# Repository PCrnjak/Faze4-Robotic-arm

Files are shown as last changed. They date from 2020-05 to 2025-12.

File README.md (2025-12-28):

   
# Faze4-Robotic-arm

 

https://source-robotics.com

Join discord community: https://discord.com/invite/prjUvjmGpZ 
Faze4 is small fully 3d printable Open source 6 axis robotic arm. It is functionally and esthetically similar to robotic arms in industry but is aimed for research, education and 
anyone interested in making his own robot arm. 
Main "selling points" of this arm that separate it from other DIY arms are:

* It is cheap <1000 dollars.
* Uses 3D printed cycloidal gearboxes which have low backlash and can be repaired really easy.
* All wires are hidden giving it clean design.

Whole arm has around 1000 parts (including screws and bearings) and weights around 15 kg.

# Check the arm in action!
Check the arm in action ! (https://www.youtube.com/watch?v=ye37Mpj5qCQ)

# Where to start? 

To build this robotic arm follow [Building instructions](https://github.com/PCrnjak/Faze4-Robotic-arm/blob/master/Assembly%20instructions%203.1.pdf). All general info about robotic arm is in [DOCS](https://faze4-robotic-arm-docs.readthedocs.io/en/latest/). Building instructions and DOCS go hand in hand and you need to follow both to build this arm. Building instructions are about general mechanical assembly while DOCS contain ALL info ( Electrical wiring, Low level setup, High level ROS and Matlab, tips ...).

# Contents:

- [Building instructions](https://github.com/PCrnjak/Faze4-Robotic-arm/blob/master/Assembly%20instructions%203.1.pdf)
- [BOM](https://github.com/PCrnjak/Faze4-Robotic-arm/blob/master/BOM_7_11_2023.xlsx) 
- [DOCS](https://faze4-robotic-arm-docs.readthedocs.io/en/latest/) Contains ALL info about the arm.
- [URDF files](https://github.com/PCrnjak/Faze4-Robotic-arm/tree/master/URDF_FAZE4) 

# Where to see more Faze4 robotic arm?
- [Youtube](https://www.youtube.com/channel/UCp3sDRwVkbm7b2M-2qwf5aQ)
- [Hackaday](https://hackaday.io/project/167247-faze4-robotic-arm)
- [DOCS](https://faze4-robotic-arm-docs.readthedocs.io/en/latest/)
- [Instagram](https://www.instagram.com/source_robotics/)

# ⚠️ Safety, Liability & Disclaimer

This project includes experimental software, hardware designs, and assembly documentation that are still under development and may contain bugs, errors, or incomplete features.
By using, building, or modifying this project, you acknowledge and agree that:
* You use this project entirely at your own risk
* You are solely responsible for safe assembly, testing, and operation
* No guarantee is made regarding correctness, safety, or reliability
* The authors are not responsible for any damage, injury, or loss resulting from the use or misuse of this project 
* Hardware performance and safety depend on user assembly, component quality, calibration, and handling, which cannot be guaranteed

This project is provided “as is.” If you choose to build a device yourself using these files, designs, or instructions, you do so without any warranties or guarantees, including regarding safety, reliability, or suitability for any particular purpose.

# Support the project

This project is entirely open source and free for all to use. Any support, whether through donations or advice, is greatly appreciated. Thank you!

 


# Project is under MIT Licence

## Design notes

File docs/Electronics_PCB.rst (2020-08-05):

Electronics, PCB and wiring
===========================

.. meta::
   :description lang=en: info about Electronics and PCB.
   
All electronics can also be bought from ebay and similar sites. I used cheap stepper drivers from ebay but you can buy any stepper driver that can supply enough current for the steppers.

Check how i wired my arm in this file: FAZE4 Robotic arm electronics setup.pdf on github page:
https://github.com/PCrnjak/Faze4-Robotic-arm

.. Tip::

   From experience i found out that cheaper stepper drivers tend to make more noise, so if you want quiet robot arm buy more expensive drivers. I found ones from stepperonline good.

PCB V1
------------
This PCB is first version and has some errors that will be fixed in revision 2.
Board was created in Altium Circuitmaker and all files can be found here:

.. Warning::

  I recommend waiting for next version since this one has alot of errors.

* `All files for PCB`_

.. _All files for PCB: https://github.com/PCrnjak/Faze4-Robotic-arm/blob/master/Distribution_PCB.zip

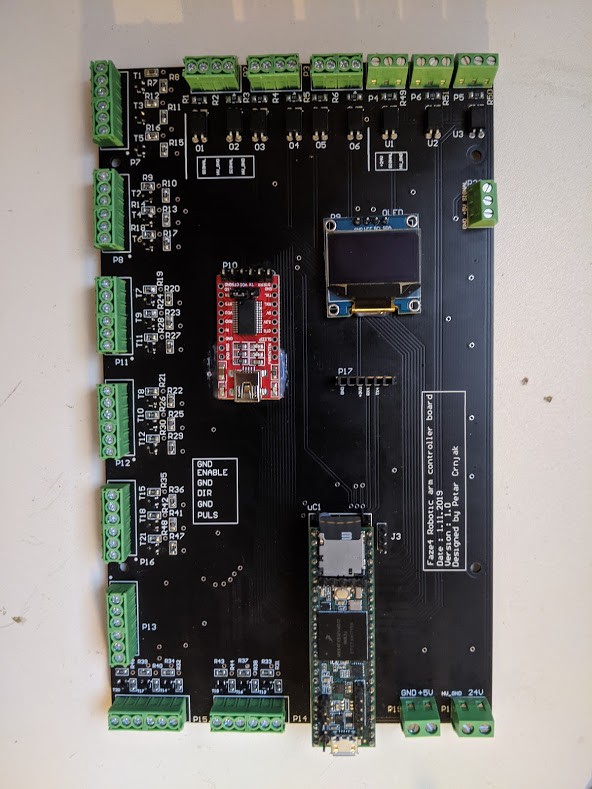
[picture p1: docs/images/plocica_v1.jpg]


Upper section of PCB are Inputs for limit switches and inductive sensors. All inputs on top are isolated with optocouplers. I did that since all wires of the arm are going thru same spot, that means "high voltage" stepper wires were near low voltage limit switch wires. That caused problems where steppers induced enough voltage on limit switch wires to trigger interrupts on teensy. That is why limit switches and sensors are connected to 24v.

left side is for stepper outputs. There are also 2 stepper outputs on bottom right side.

Bottom right side has 5V input and 24V input. You need both for arm to work. In the middle we have few extra serial ports and OLED display.

When wiring stepper drivers to the PCB i used TB6600  driver pinout as reference.I planned for all drivers to be connected like picture below. HIGH signal on ENABLE + pin would enable stepper drivers. Now i made some mistakes and not all drivers can be connected like that.

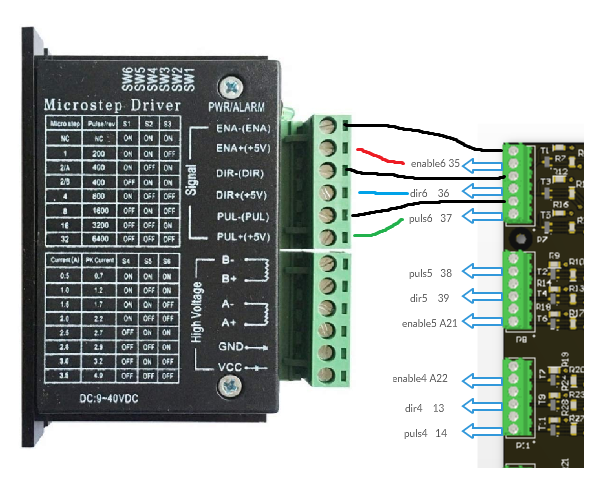
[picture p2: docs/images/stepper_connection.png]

    
Now i made some mistakes and not all drivers can be connected like that. In picture below you can see how to connect all drivers. As you can see for joint 5 (connector below top one) i switched enable and puls pins. That means that puls5 pin ( pin 38 on teensy) is connected to puls pin on stepper driver. I also skipped Port that has no 5V level shifter since it didnt work well.

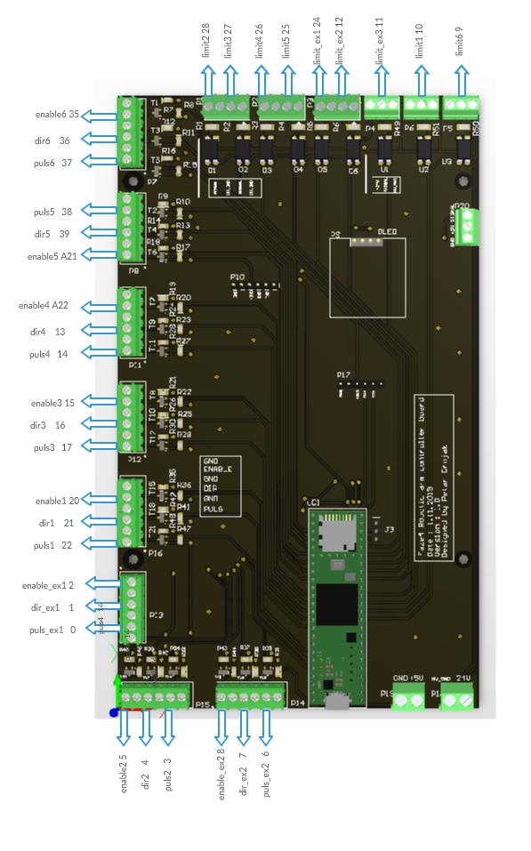
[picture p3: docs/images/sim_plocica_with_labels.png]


After wiring all dir,puls and enable pins you are left with power pins on stepper driver and A- A+ B- B+ Pins. Those are quite straightforward. 
Pins that have ext in name are extra pins that are now used in my version of arm.

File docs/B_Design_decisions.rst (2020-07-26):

Design decisions
===========================

.. meta::
   :description lang=en: Design decisons that were made when designing faze4 arm.

Number of axis
--------------

I went with 6 axis because with 6+ axis we can reach same dot in space with different orientations.
Both pictures show arm at position x=0.3m , y=0.3m and z=0.2m but as you can see orientations are different. 

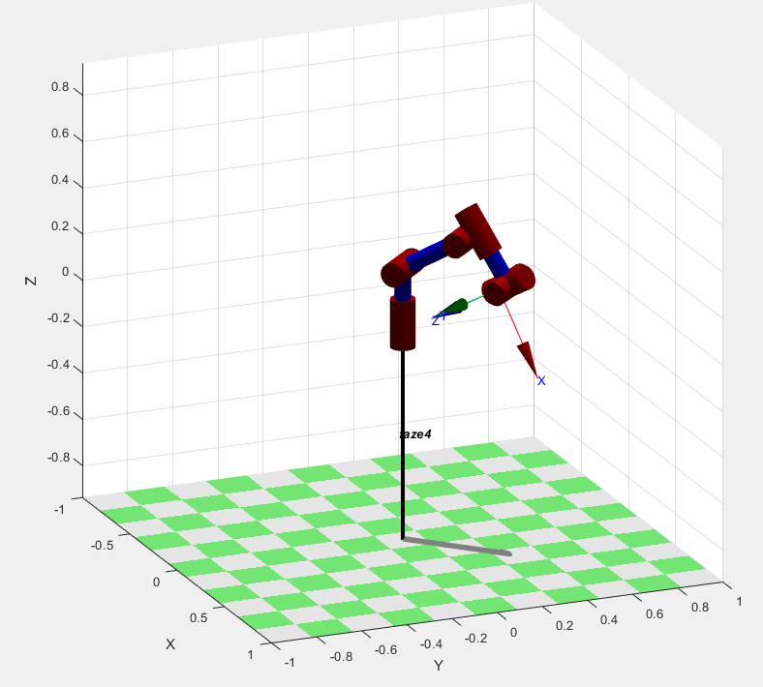
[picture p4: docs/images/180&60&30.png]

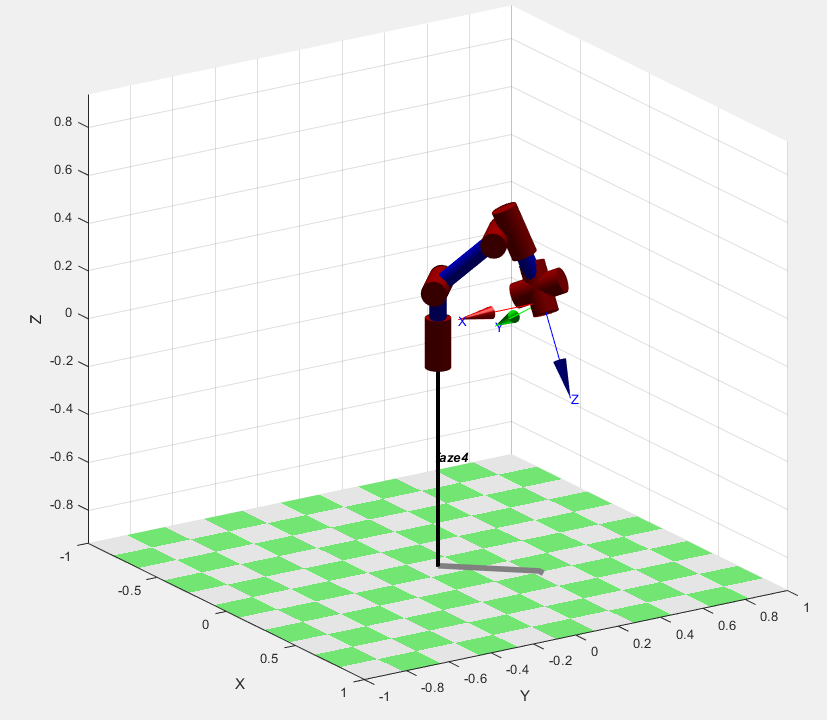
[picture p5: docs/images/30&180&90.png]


Spherical wrist
---------------

This arm uses so called spherical wrist. Spherical wrist is configuration of joints where axes of rotation for joints 4,5,6 intersect.
You can see that in picture below. It is complicated mechanical system that in turn simplifies solving inverse kinematics for robot arm. You will see this configuration in a lot industrial robot arm. 

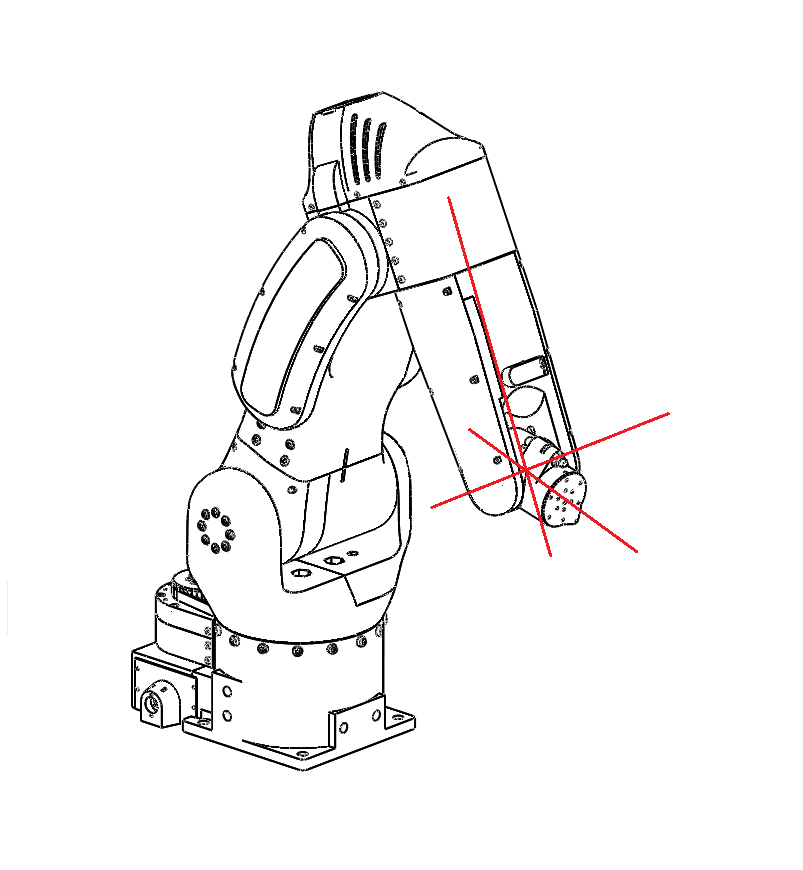
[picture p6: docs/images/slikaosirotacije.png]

    
All wires are routed thru the middle of the arm and cant be seen.

Cycloidal reducer
-----------------

Why cycloidal reducers?

* They are really easy to 3d print
* can have large reduction ratio
* cheap
* low backlash even when 3d printed

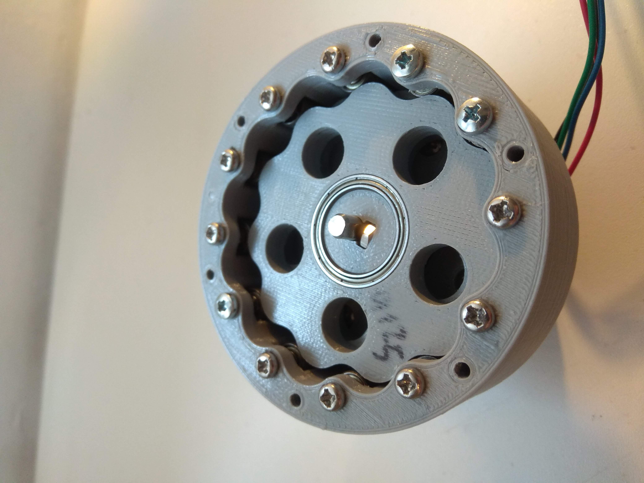
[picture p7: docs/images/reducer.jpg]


.. note::
   When 3d printing them there are few things to keep in mind but that is discussed in sections troubleshooting and printing.

Motor position
--------------

Firstly i wanted to move all motors to the base of the arm to reduce weight each motor should carry. First idea was to just copy the design of this(link) kuka arm. I decided against that design and just went with probably most basic design where every motor is directly on the joint of actuation ( Except for joint 5 that i moved a little bit away).This is not good idea actually and if I was redesigning this arm I would try to move at least joint 3 to the bottom of the arm, but what is done is done.

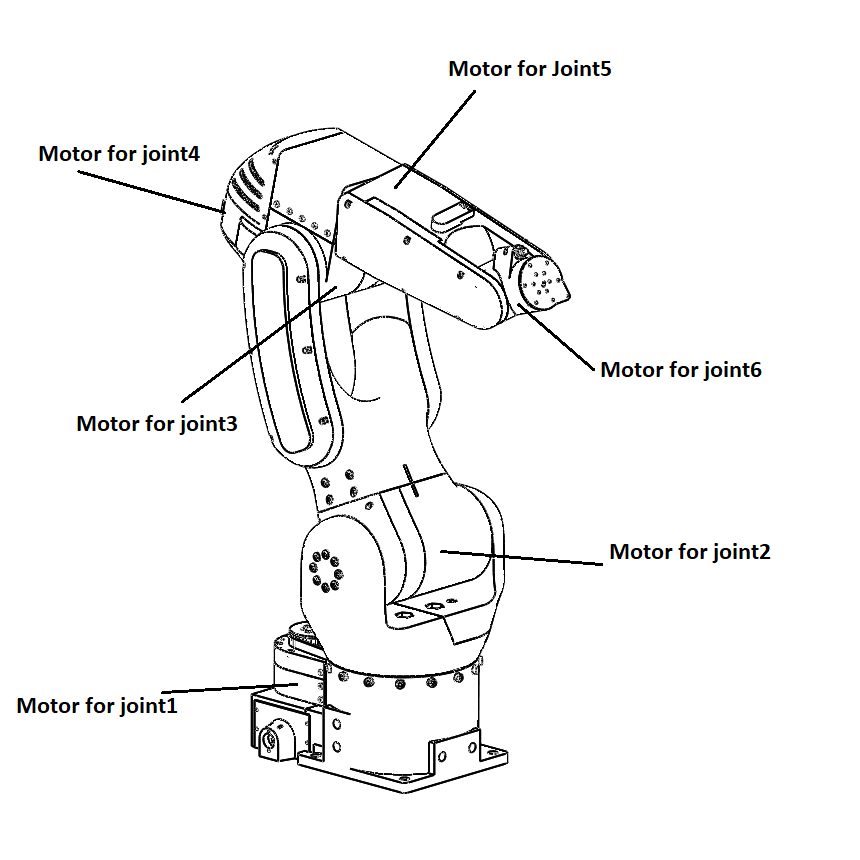
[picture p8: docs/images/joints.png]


Joints 1,4 and 5 use belts in addition to cycloidal reducers. Belts are mostly used to offset the place where joint will be rotating so that we can route wires thru the body of robot. They also give some additional reduction ratio. For example Joint 1 has 15:1 cyclo but with belt our reduction ratio jumps to 25:1.

Reduction ratios:
-----------------

* Joint 1 -> 15:1 cycloidal reducer and 5:3 belt reduction = combined resulting in 25:1 reduction
* Joint 2 -> 27:1 cycloidal reducer
* Joint 3 -> 15:1 cycloidal reducer
* Joint 4 -> 11:1 cycloidal reducer and 28:26 belt reduction = combined resulting in 11.846153:1 reduction 
* Joint 5 -> 11:1 cycloidal reducer and 1:1 belt reduction = combined resulting in 11:1 reduction
* Joint 6 -> 19.19:1 planetary reducer

Belts
-----------------

* Joint 1 belt is HTD 5M 490 mm timing belt 10 mm wide and needs to be tightened with bearings
* Joint 4 belt is HTD 5M 430 mm timing belt 10 mm wide does not need to be tightened
* Joint 5 belt is HTD 5M 285 mm timing belt 10 mm wide and needs to be tightened with bearings

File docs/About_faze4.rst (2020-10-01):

About Faze4
===========================

.. meta::
   :description lang=en: General info about Faze4 robotic arm.

General info
------------

Faze4 robotic arm came to be when i made a working 3d printable cycloidal gearbox and saw some potential in it. After that i designed whole arm around it. It uses 6 stepper motors, so it is a 6 axis robot arm. While designing this arm i focused on low backlash and good design of arm. All wires are hidden and arm is really rigid even tho it is 3d printed. Total cost of the arm is around 1000 - 1500 dollars.

.. note::

    This project is still work in progress. Part that is work in progress is control cabinet, that means that the arm can be built and it     will work without the cabinet.
    
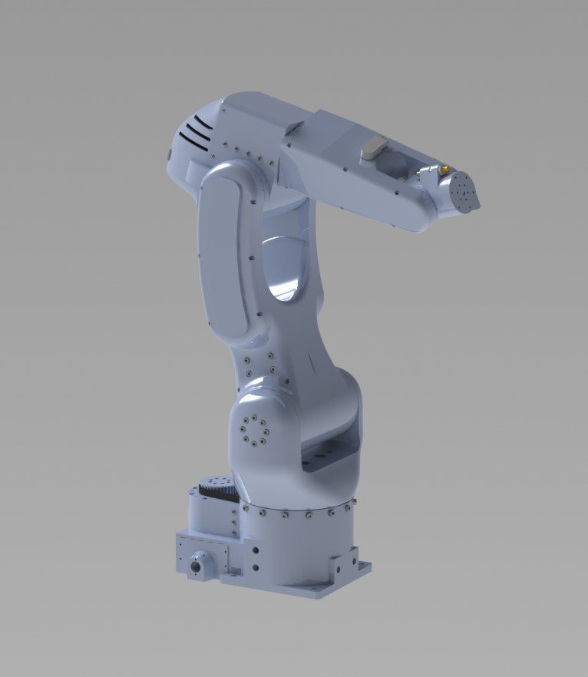
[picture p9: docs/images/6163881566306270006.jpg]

    
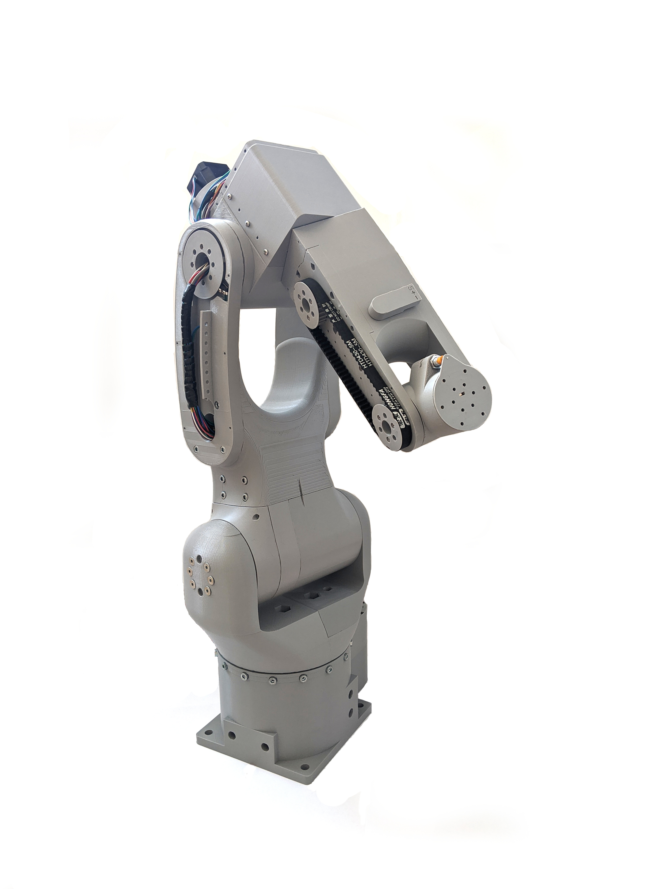
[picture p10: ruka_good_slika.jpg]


Esthetic design was inspired by FANUC’s LR Mate 200iD. 
Goal was also to hide all wires in the arm like most industrial arms do. 
Only visible wires (or pipes) would be ones for gripper. 

Weight of the arm is around 14-15 kg , but it can be reduced by printing with less infill.

Low level control for the arm runs on teesny 3.5, while high level (inverse kinematics, simulations) are only on Matlab code atm, but I am working on ROS implementation and porting my Matlab code to Python.

Table of contents
-----------------

On this read the docs page you will find:

* How is arm desinged and desing decisions
* Printing tips
* Electronics guide and PCB
* Building instructions for the arm
* All code and programs used
* How to test and troubleshoot
* Sources 
* Where to buy parts

Check the arm in action !
-------------------------

.. raw:: html

    <div style="text-align: center; margin-bottom: 2em;">
    <iframe width="100%" height="350" src="https://www.youtube.com/embed/-qTVx23o6C0?rel=0" frameborder="0" allow="autoplay; encrypted-media" allowfullscreen></iframe>
    </div>

Support the project
-------------------

This project is completely Open source and free to all and I would like to keep it that way, so any help 
in terms of donations or advice is really appreciated. Thank you!

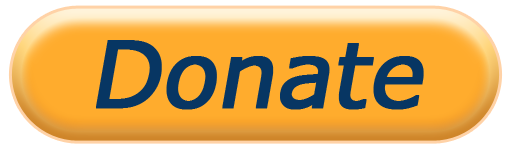
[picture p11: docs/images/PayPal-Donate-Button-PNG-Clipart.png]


Thanks to the:
--------------
* `Peter Corke for his amazing robotics toolbox for Matlab`_
* `Maximilian_Schommer for his cycloidal drive generator`_

.. _Peter Corke for his amazing robotics toolbox for Matlab: https://petercorke.com/toolboxes/robotics-toolbox/
.. _Maximilian_Schommer for his cycloidal drive generator: https://forum.onshape.com/discussion/7567/cycloidal-gear-generator

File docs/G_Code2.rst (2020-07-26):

High level code
===========================

.. meta::
   :description lang=en: info about Code.
   
High level code does all calculations and simulations. It will usually run on the PC since it will be doing a lot of
math and matrix multiplications. It will use some kind of inverse kinematics solver that will generate joint angles and speeds.
Again, gross simplification, but we will talk more about it later.

All code is in github repository.

Matlab code for testing in live script
---------------------------------------

 Matlab trajectory planning
----------------------------

ROS  
----

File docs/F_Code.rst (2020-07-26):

Low level code
===========================

.. meta::
   :description lang=en: info about Code.
   
Code for this robotic arm can be devided in 2 parts:

* Low level code
* High level code

Low level code is code that runs on our microcontroller (in our case teensy 3.5).
Its main purpose is to receive information from high level code and transform that information 
into useful signals for stepper drivers. That is a gross simplification, but codes used 
will be explained in more detail below.

All code is in github repository.

Tennsy environment setup
------------------------

Teensy low level code for testing in Matlab(live script)
--------------------------------------------------------

Teensy low level code for Matlab trajectory planning
----------------------------------------------------

Teensy low level code for ROS 
-----------------------------

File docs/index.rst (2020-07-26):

.. Read the Docs documentation master file, made by Petar Crnjak.

Faze4 Robotic arm documentation
==================================================

Contents:

.. toctree::
   :maxdepth: 2
   :glob:

   *

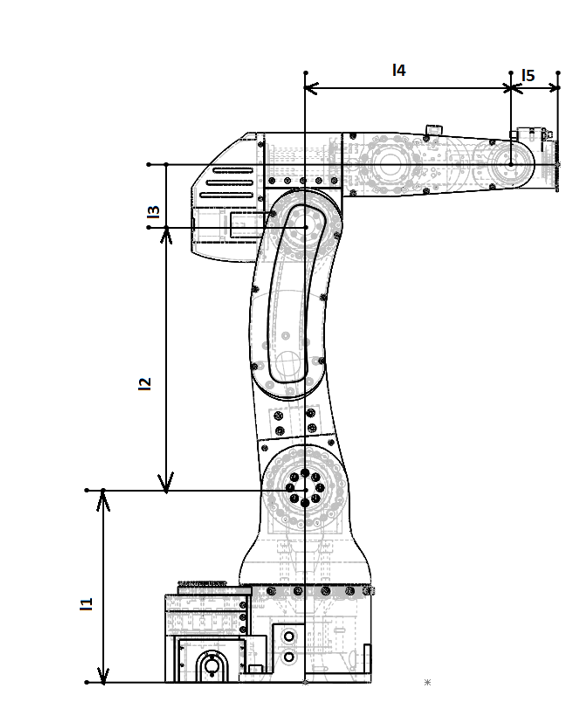
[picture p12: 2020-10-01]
docs/images/robot_dim.png

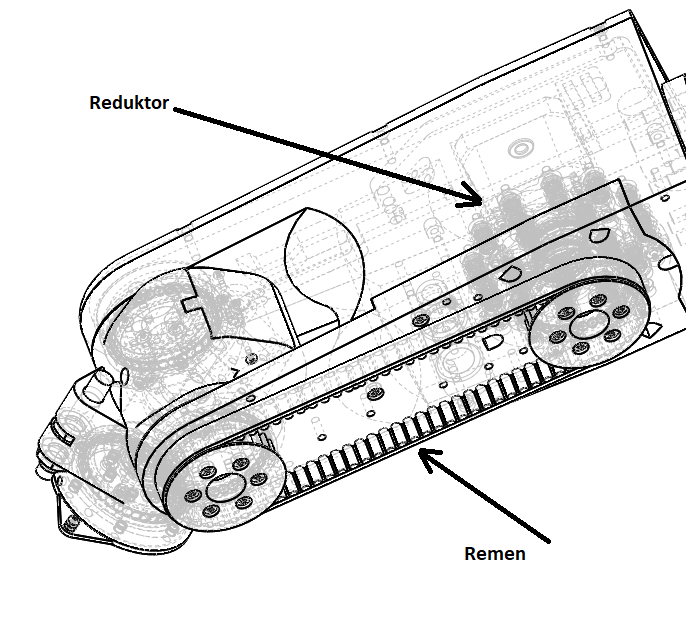
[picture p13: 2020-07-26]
docs/images/ReduktorREMEN.png

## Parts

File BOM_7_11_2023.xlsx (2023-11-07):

Some links included are affiliate links!
Screws: |  |  | 3D Printed parts:
diameter , lenght | Type | quantity | Name | quantity
M2 5mm screw | philips pan head | 3 | Joint 6 Output shaft | 1
M3 5mm screw | philips pan head | 12 | Wrist case | 1
M3 4mm set screw | Hex | 6 | Wrist cover | 1
M3 25mm screw | philips pan head | 64 | Forearm main case | 1
M2 8 mm screw | philips pan head | 8 | J5 ring rollers | 12
M3 20mm screw | philips pan head | 53 | 11:1 cyclo disc | 4
M3 10 mm screw | philips pan head | 54 | Eccentric shaft J5 | 1
M3 15mm screw | philips pan head | 54 | Servo gripper plug | 1
M5 30 mm screw | Hex socket cap | 13 | joint 5 output shaft | 1
M5 20 mm screw | Hex socket cap | 27 | joint 5 output spacers | 10
M5 8 mm screw | Hex socket cap | 12 | joint 5 switch trigger | 1
M3 30 mm screw | philips pan head | 52 | Forearm top cover | 1
M5 25 mm screw | Hex socket cap | 8 | J5 28 teeth pulley | 2
M2 10-12 mm screw | philips pan head | 7 | Joint 4 output shaft | 1
M5 40 mm screw | Hex socket cap | 10 | Joint 4 motor case | 1
M10 60 mm screw | Hex socket cap | 4 | J4 ring spacers | 12
 |  |  | Eccentric shaft J4 | 1
 |  |  | J4 cyclo output shaft | 1
 |  |  | joint 4 output spacers | 10
Bearings: |  |  | Joint 4 top cover | 1
Type | quantity | Link | Joint 3 main case | 1
Ball bearing 35x47x7 | 8 | Link (https://s.click.aliexpress.com/e/_DEiQvOn) | Joint 3 cover | 1
Ball bearing 3x8x4 | 200 | Link (https://s.click.aliexpress.com/e/_DdsVB2J) | 15:1 cyclo disc | 4
Ball bearing 17x23x4 | 4 | Link (https://s.click.aliexpress.com/e/_DExAkpt) | Joint 3 ring spacers | 32
Ball baering 15x28x7 | 6 |  | Joint 3 eccentric shaft | 1
Ball bearing 3x10x4 | 40 | Link (https://s.click.aliexpress.com/e/_Dl8fYKj) | Joint 3 output shaft | 1
Ball bearing 50x65x7 | 8 | Link (https://s.click.aliexpress.com/e/_DDV5uWF) | Joint 3 top cover | 1
Ball bearing 5x10x4 | 32 | Link (https://s.click.aliexpress.com/e/_DC7M02L) | Joint 4 offset | 1
Ball bearing 5x16x5 | 13 | Link (https://s.click.aliexpress.com/e/_Dl0Pgbd) | Joint 4 limit switch cover | 1
Ball bearing 20x27x4 | 2 | Link (https://s.click.aliexpress.com/e/_DCazrFD) | Joint 4 pulley 28 teeth | 1
 |  |  | 26 teeth Joint 4 pulley | 1
Other: |  |  | Fork | 1
Name | quantity | Link | Fork_motor | 1
M3 4mm brass inserts | 12 |  | Fork_wires | 1
M2 nuts | 2 |  | Joint 3 limit trigger | 1
M3 nuts | 6 |  | Joint 2 main case | 1
Inductive sensor | 2 | Link (https://s.click.aliexpress.com/e/_DE9VnjZ) | Joint 2 cover | 1
M8 nuts (usually included with sensor | 4 |  | Joint 2 eccentric shaft | 1
Nema 14 L=33mm w/19:1 gearbox | 1 | Link (https://www.omc-stepperonline.com/nema-14-stepper-motor-bipolar-l-33mm-w-gear-ratio-19-1-planetary-gearbox-14hs13-0804s-pg19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) | Joint 2 cyclo disc | 2
Nema 17 Bipolar 12V 42x42x40mm | 2 | Link (https://www.omc-stepperonline.com/nema-17-bipolar-45ncm-64oz-in-2a-42x42x40mm-4-wires-w-1m-cable-connector-17hs16-2004s1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) | Joint 2 ring spacer | 28
Pneumatic bulkhead connector 4mm xM12 thread | 2 |  | Joint 2 output shaft | 1
M12 nuts | 4 |  | Joint 2 top cover | 1
4mm pneumatic tube | 1 |  | Rotating base wires | 1
Micro limit switch | 3 |  | Rotating base motor | 1
HTD 5M 430 mm timing belt 10 mm wide | 1 |  | Joint 1 output shaft | 1
Nema 23 Bipolar 0.9deg 2.8A 2.5V 57x57x56mm | 1 | Link (https://www.omc-stepperonline.com/nema-23-bipolar-0-9deg-1-26nm-178-4oz-in-2-8a-2-5v-57x57x56mm-4-wires-23hm22-2804s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) | Joint 1 main case | 1
J4 beltv = HTD belt 5M 285 10mm wide | 1 |  | Joint 1 cover | 1
Nema 23 Bipolar 4A 2.26V 57x57x84mm | 1 | Link (https://www.omc-stepperonline.com/dual-shaft-nema-23-uni-bipolar-1-8deg-2-83nm-400-oz-in-4a-57x84mm-8-wires-23hs33-4008d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) | Joint 1 ring spacers | 32
M5 nuts | 15 |  | Joint 1 eccentric shaft | 1
M10 nuts | 4 |  | Joint 1 cyclo output shaft | 1
Roller limit switches | 2 |  | Joint 1 top cover | 1
Nema 23 Bipolar 1.5A 5.4V 57x57x56mm | 1 | Link (https://www.omc-stepperonline.com/nema-23-bipolar-1-8deg-1-16nm-164-3oz-in-1-5a-5-4v-57x57x56mm-4-wires-23hs22-1504s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) | Main base | 1
HTD 5M 490 mm timing belt 10 mm wide | 1 |  | 36 teeth pulley | 1
 |  |  | Ball bearing retainer | 1
 |  |  | Shaft blocker | 1
 |  |  | Forearm motor lid | 1
Total not 3d printed parts : | 764 |  | Forearm wires lid | 1
 |  |  | Elbow lid | 1
Total 3d printed parts : | 197 |  | Upper arm lid | 1
 |  |  | Rotating base lid | 1
Total parts | 961

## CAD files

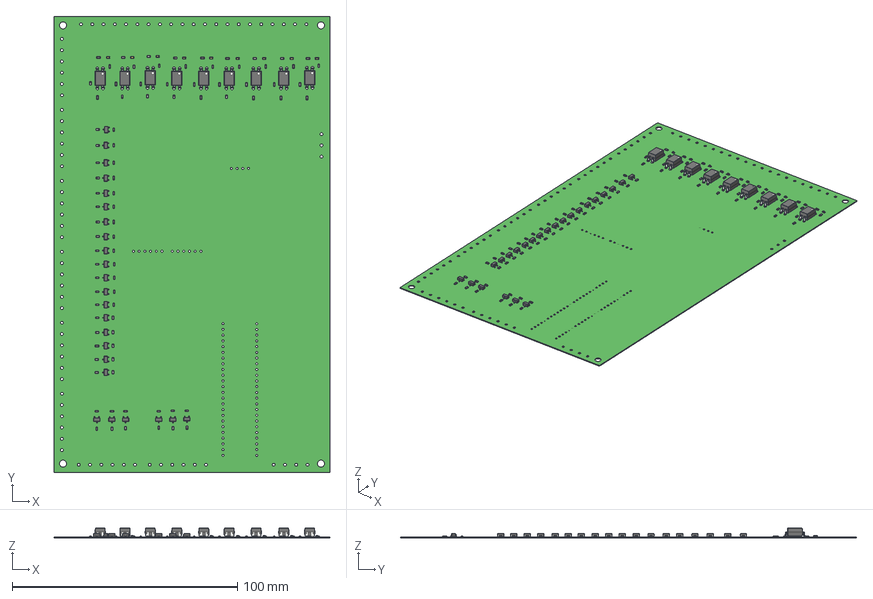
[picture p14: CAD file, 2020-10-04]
Faze4_DIST_board_v2_files/Faze4_dist_v2_STEP.step
122.5 x 202.5 x 4.26 mm
Board
0603_resistor x 84
LTV-817S x 9
LED_0603_Base_YELLOW x 9
LED_0603_Lens_YELLOW x 9
sot-23-3 x 24

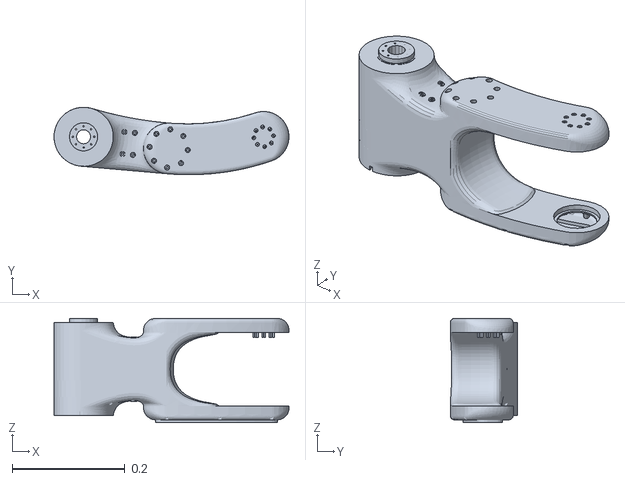
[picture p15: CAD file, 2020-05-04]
URDF_FAZE4/meshes/nadlaktica.STL
0.417 x 0.12 x 0.185

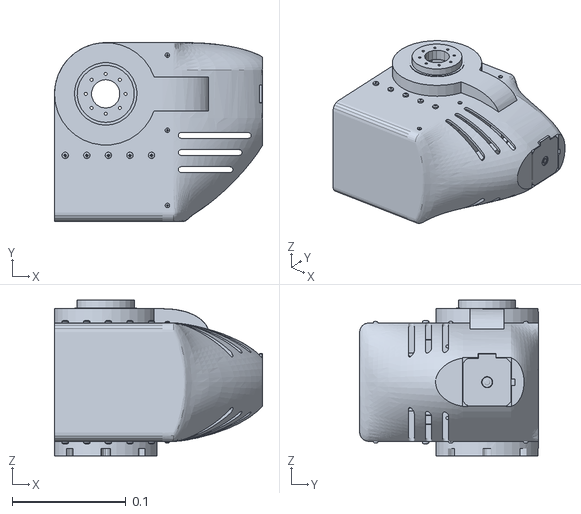
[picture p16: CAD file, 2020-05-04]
URDF_FAZE4/meshes/lakat.STL
0.183 x 0.157 x 0.137

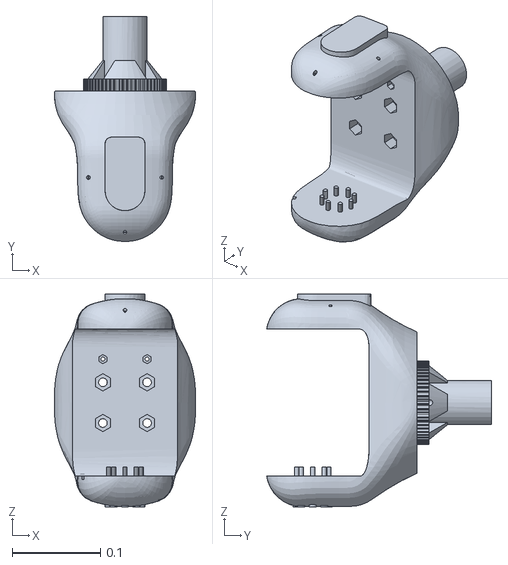
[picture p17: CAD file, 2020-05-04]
URDF_FAZE4/meshes/rotary_base.STL
0.16 x 0.254 x 0.241

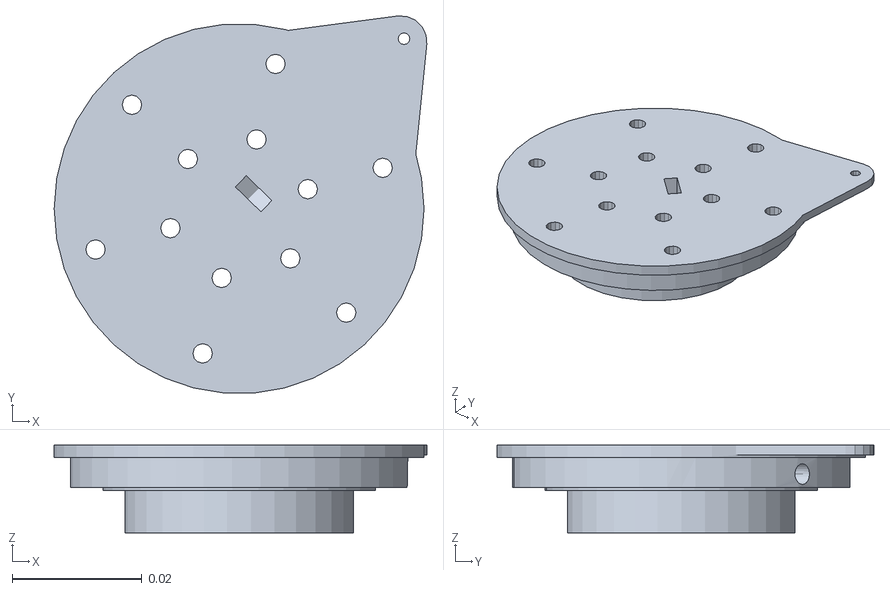
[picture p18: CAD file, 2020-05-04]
URDF_FAZE4/meshes/hvataljka.STL
0.0574 x 0.0581 x 0.0135

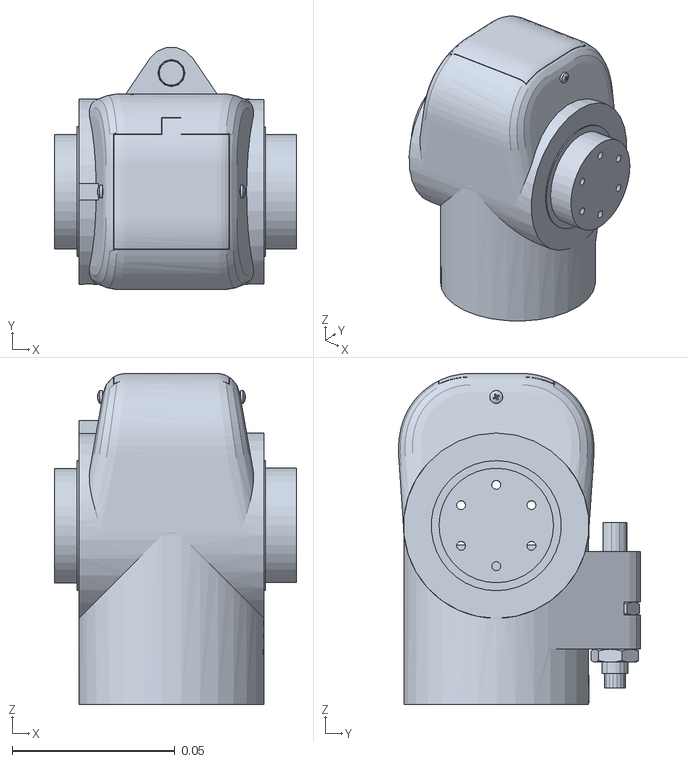
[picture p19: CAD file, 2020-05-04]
URDF_FAZE4/meshes/saka.STL
0.0745 x 0.0744 x 0.102

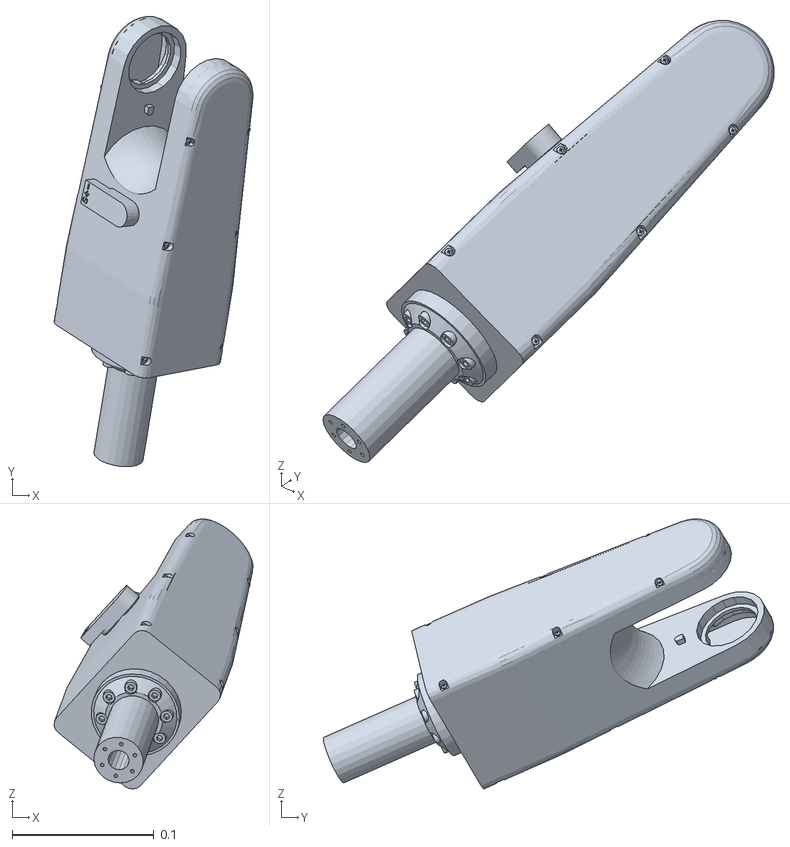
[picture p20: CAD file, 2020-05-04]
URDF_FAZE4/meshes/podlaktica.STL
0.14 x 0.318 x 0.191

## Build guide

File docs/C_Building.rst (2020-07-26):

Building 
===========================

.. meta::
   :description lang=en: Instructions and tips to build mechanical part of the arm.
   
.. note::

   All parts can be bought from ebay and similar online stores. I bought all steppers,drivers and PSUs from stepper online. You can buy    screws used for this arm in online stores but i sourced them locally and that was much cheaper. I also recommend to buy wires (you      will need them to extend stepper wires) locally since ones on ebay and similar stores are of questionable quality.

* `Full assembly instructions are here`_

.. _Full assembly instructions are here: https://github.com/PCrnjak/Faze4-Robotic-arm

BOM
------------
You can find bom in this excel document and in building instructions file. 

* `BOM FILE`_

.. _BOM FILE: https://github.com/PCrnjak/Faze4-Robotic-arm

.. Tip::

   I also recommend to buy more items like bearinngs and screws than you need since you might destroy or damage some in building            process.

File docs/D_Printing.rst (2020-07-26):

Printing
===========================

.. meta::
   :description lang=en: Printing tips.

Filament
------------

I recommend PETG since it can withstand larger temperatures then PLA and is easier to print then ABS. Since motors can heat up i think it is best choice.

Printer
------------

All parts are designed to be printed on Prusa MK2S, so if you have printer with build volume of 250x210x200 you are good to go.

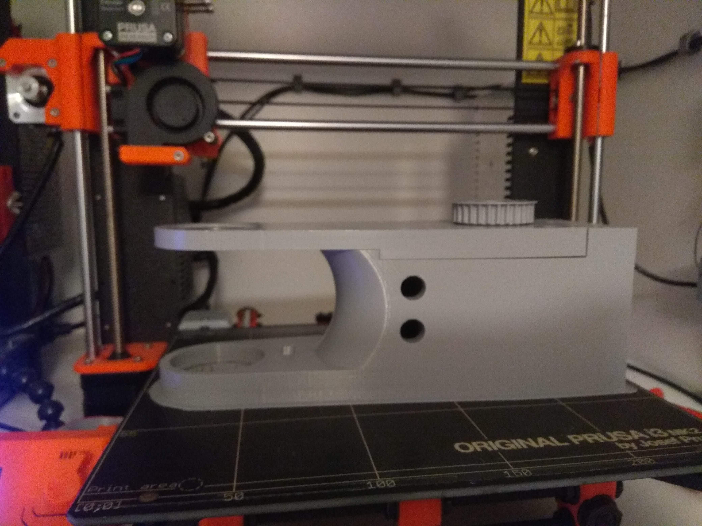
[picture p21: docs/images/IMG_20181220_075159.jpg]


Print settings and tips
------------------------

I printed all smaller parts with 0.15 layer height and all larger with 0.35 layer height.For infill try to stay in 25%-30% range. I used 3 outer perimeters and 7 top and 5 bottom layers.

.. Tip::

   When printing larger parts like: x x x , try to print at slower speeds and with small accelerations.Since those parts are really        large and heavy they tend to cause missing steps when reaching the end of 3d print due the inertia.

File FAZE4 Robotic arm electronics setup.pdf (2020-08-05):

FAZE4 Robotic arm electronics setup

So this is wiring guide for my setup of the arm. If you plan to build Faze4 robotic arm it might not look like this. Your wires might have different colour coding, different steppers…
So here i am going to explain some general tips.
- Microsteps for motors should be kept like ones in tables. If you change them change microstep values in software to.
- Adjust Peak current for your steppers. I used peak value of stepper drivers but actually we use RMS value of current so adjust to your RMS current!
- Voltage your stepper motor is rated
- Limit switch dir tells us what state needs to be on stepper driver DIR pin to initiate movement in DIRECTION TO HIT A LIMIT SWITCH ! This is really important! These values should be left as they are in this table. If you see your stepper is moving away from limit switch just switch any 2 wires of the same phase on stepper driver and that will change the direction. You can change it in software too but this method is easier.
- ENABLE tells us what state on enable pin of stepper drivers ENABLES the driver.
- Wires for my setup and Control pins are specific for my build of the arm.

ROBOT electronics setup

JOINT 6

Microstep | Current | Voltage | Limit switch DIR | ENABLE
400 | PK 0.7A | 24V | LOW | LOW

Wires for my setup: red,green,blue,yellow (A+,A-,B+,B-)
Control pins: GND,ENA+,GND,DIR+,PULS+

JOINT 5

Microstep | Current | Voltage | Limit switch DIR | ENABLE
400 | PK 1.2A | 24V | HIGH | ANALOG: 0

Wires for my setup: red,blue,green,black (A+,A-,B+,B-)
Control pins: GND,PULS+,GND,DIR+,ENA+

JOINT 4

Microstep | Current | Voltage | Limit switch DIR | ENABLE
400 | PK 1.2A | 24V | HIGH | ANALOG: 0

Wires for my setup: red,blue,black,green (A+,A-,B+,B-)
Control pins: GND,ENA+,GND,DIR+,PULS+

JOINT 3

Microstep | Current | Voltage | Limit switch DIR | ENABLE
400 | PK 2.2A | 24V | HIGH | LOW

Wires for my setup: red,blue,black,green (A+,A-,B+,B-)
Control pins: GND,ENA+,GND,DIR+,PULS+

JOINT 2

Microstep | Current | Voltage | Limit switch DIR | ENABLE
1600 | PK 2.7A | 36V | HIGH | LOW

Wires for my setup: red,yellow,orange,purple (B-,B+,A-,A+)
Control pins: PULS+,GND,DIR+,GND,ENA+

JOINT 1

Microstep | Current | Voltage | Limit switch DIR | ENABLE
1600 | PK 2.7A | 24V | HIGH | LOW

Wires for my setup: red,blue,black,green (A+,A-,B+,B-)
Control pins: GND,ENA+,GND,DIR+,GND,PULS+

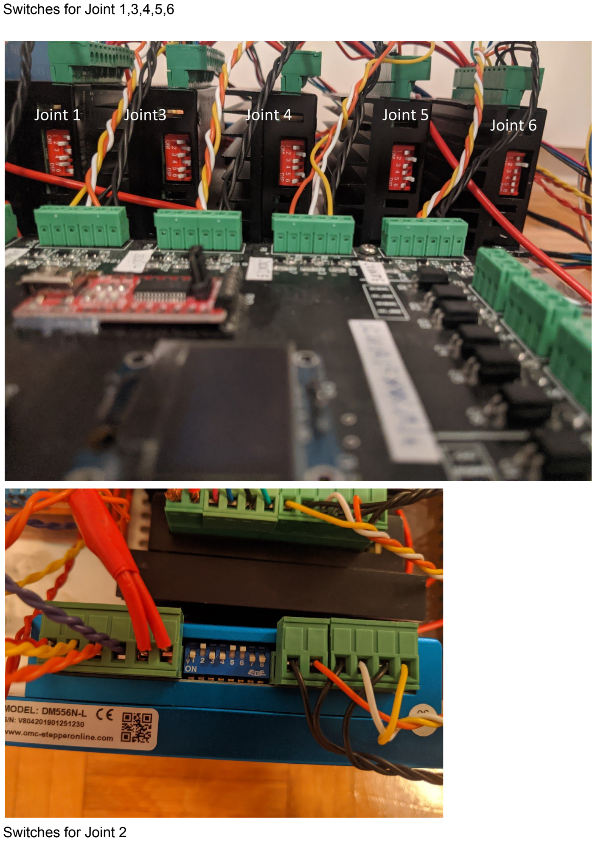
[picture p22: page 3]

Switches for Joint 1,3,4,5,6

Switches for Joint 2

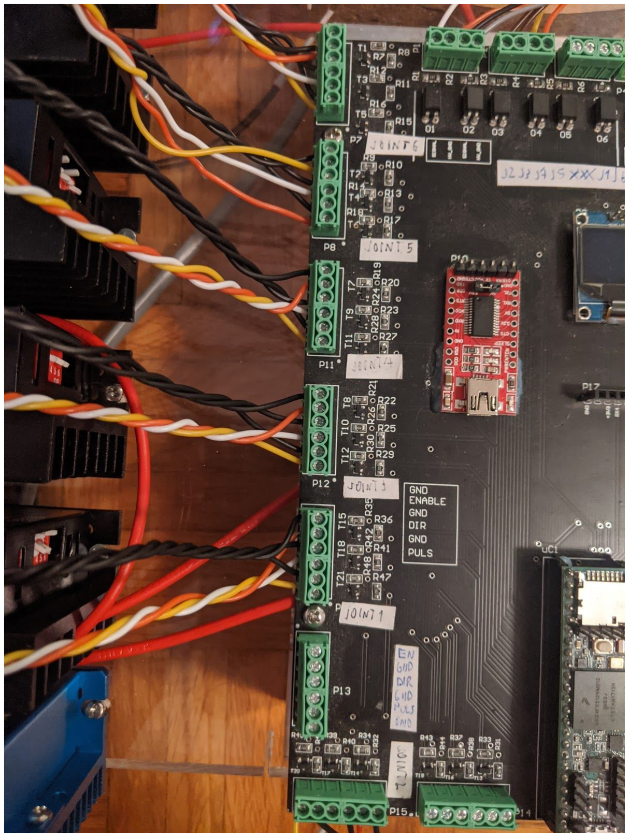
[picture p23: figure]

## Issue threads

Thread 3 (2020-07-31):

high-level help

i-make-robots, 2020-07-31:
Hi!  Your arm is gorgeous.  Would love to see some exploded diagrams or section diagrams in the documentation.

I have a visual simulator and firmware that should run IK for your robot and knows how to use acceleration for smoother motion.

https://github.com/MarginallyClever/Makelangelo-software is the firmware (supporting many kinematic models) and

https://github.com/MarginallyClever/Robot-Overlord is the software (gradient descent IK, simulation, etc)

I hope it helps!

PCrnjak, 2020-09-06:
I am really sorry i didnt see this. Yea i saw your robot - overlord software and i am planning to try it out, but first i want to get ROS working so it will take some time.
Anyway when i start working on it i will keep you updated, it looks great thx!

Closed 2024-03-13.

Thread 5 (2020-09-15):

thanks for your work

maokk, 2020-09-15:
I am almost print all the STL files and prepare for assemble . waiting for your low and high code release, thank you

Closed 2024-03-13.

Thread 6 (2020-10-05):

Wrong Bearing in BOM

Waldkaeuzchen, 2020-10-05:
Hello,
first off all, thank you for your amazing Work!

While searching for all parts I noticed that their seems to bin a Typo in the list: the ball bearings 50x67x7 are listed, but later on in the manual 50x65x7 is used, which doesnt appear in the BOM.

Greetings,
Waldkaeuzchen

Closed 2024-03-13.

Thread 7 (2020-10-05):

Building instructions link broken

maxymczech, 2020-10-05:
https://github.com/PCrnjak/Faze4-Robotic-arm/blob/master/Assembly%20instructions%203.0.pdf - this link in readme.md is 404 broken.

Closed 2024-03-13.

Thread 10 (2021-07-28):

STEP Files

MaxBareiss, 2021-07-28:
This robot arm is awesome and I'm trying to make one. Inductive sensors with an 8mm body are too expensive, so I bought ones with an 18mm body and I'd like to adapt the parts to the new hole size. Are the original CAD files or STEP format CAD files publically available for this project to make it easier to modify?

maokk, 2022-02-18:
I am also have  the  same problem, I am prepare to assemble this robot arm, but my joint3 stepper motor are a little bit different , its very ugly to cut after printed the Joint 3 cover.STL

Closed 2024-03-13.

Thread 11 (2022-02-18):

question about Joint 3 cover.STL

maokk, 2022-02-18:
thanks for your great job, I am now prepare to assemble this robot arm, but my joint3 stepper motor are a little bit different from yours, its very ugly to cut after printed the "Joint 3 cover.STL", so could you share this modified file? thanks

Closed 2024-03-13.

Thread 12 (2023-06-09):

Wild mesh origins

i-make-robots, 2023-06-09:
Hi!

I loaded the meshes into Robot Overlord today and I see the mesh origins are all over the place.  I'm unable to fix the files using the URDF numbers.

I would like please:

1. all arm parts share the same origin at the robot base center

OR

2. all arm parts have their correct local origin with Z axis matching the axis of rotation.

... and a DH parameter table that includes max/min joint range, D, R, Alpha, and Theta.

Example of wonky origin attached.  This model is also some distance off the floor.
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

Closed 2024-03-13.

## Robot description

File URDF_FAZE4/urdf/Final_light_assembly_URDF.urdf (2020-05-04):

<robot name="Final_light_assembly_URDF">
  <link name="base_link">
    <inertial>
      <origin xyz="0.0754452420016786 0.0706653851885525 0.174716050606158" rpy="0 0 0" />
      <mass value="1.75590983031249" />
      <inertia ixx="0.0106901651591523" ixy="1.2533292416581E-05" ixz="-1.78802486116636E-05" iyy="0.0121389538778755" iyz="-0.0001726147454493" izz="0.00523087609446992" />
    </inertial>
    <visual>
      <origin xyz="0 0 0" rpy="0 0 0" />
      <geometry>
        <mesh filename="package://Final_light_assembly_URDF/meshes/base_link.STL" />
      </geometry>
      <material name="">
        <color rgba="0.792156862745098 0.819607843137255 0.933333333333333 1" />
      </material>
    </visual>
    <collision>
      <origin xyz="0 0 0" rpy="0 0 0" />
      <geometry>
        <mesh filename="package://Final_light_assembly_URDF/meshes/base_link.STL" />
      </geometry>
    </collision>
  </link>
  <link name="rotary_base">
    <inertial>
      <origin xyz="3.6594E-07 -0.12491 -0.0091222" rpy="0 0 0" />
      <mass value="1.8968" />
      <inertia ixx="0.011703" ixy="6.2683E-07" ixz="2.7765E-07" iyy="0.010005" iyz="-0.00096832" izz="0.0065158" />
    </inertial>
    <visual>
      <origin xyz="0 0 0" rpy="0 0 0" />
      <geometry>
        <mesh filename="package://Final_light_assembly_URDF/meshes/rotary_base.STL" />
      </geometry>
      <material name="">
        <color rgba="0.79216 0.81961 0.93333 1" />
      </material>
    </visual>
    <collision>
      <origin xyz="0 0 0" rpy="0 0 0" />
      <geometry>
        <mesh filename="package://Final_light_assembly_URDF/meshes/rotary_base.STL" />
      </geometry>
    </collision>
  </link>
  <joint name="rotary_base" type="continuous">
    <origin xyz="0.075629 -0.21266 0.050734" rpy="-1.5708 -6.123E-17 -1.5708" />
    <parent link="base_link" />
    <child link="rotary_base" />
    <axis xyz="0 -1 0" />
  </joint>
  <link name="nadlaktica">
    <inertial>
      <origin xyz="0.11187 -0.011704 0.007695" rpy="0 0 0" />
      <mass value="3.097" />
      <inertia ixx="0.011686" ixy="0.0012432" ixz="-0.0018781" iyy="0.03891" iyz="-5.4012E-05" izz="0.032612" />
    </inertial>
    <visual>
      <origin xyz="0 0 0" rpy="0 0 0" />
      <geometry>
        <mesh filename="package://Final_light_assembly_URDF/meshes/nadlaktica.STL" />
      </geometry>
      <material name="">
        <color rgba="0.79216 0.81961 0.93333 1" />
      </material>
    </visual>
    <collision>
      <origin xyz="0 0 0" rpy="0 0 0" />
      <geometry>
        <mesh filename="package://Final_light_assembly_URDF/meshes/nadlaktica.STL" />
      </geometry>
    </collision>
  </link>
  <joint name="nadlaktica" type="continuous">
    <origin xyz="0 -0.20182 0" rpy="2.7756E-15 -1.3878E-15 -1.8111" />
    <parent link="rotary_base" />
    <child link="nadlaktica" />
    <axis xyz="0 0 1" />
  </joint>
  <link name="lakat">
    <inertial>
      <origin xyz="0.020310022580536 -0.0354589471585284 0.00171229454365077" rpy="0 0 0" />
      <mass value="1.2726491805247" />
      <inertia ixx="0.00430935066273582" ixy="-0.000472663673983171" ixz="2.10793692092687E-05" iyy="0.00388873322685888" iyz="-0.000102922808916268" izz="0.00512549454697952" />
    </inertial>
    <visual>
      <origin xyz="0 0 0" rpy="0 0 0" />
      <geometry>
        <mesh filename="package://Final_light_assembly_URDF/meshes/lakat.STL" />
      </geometry>
      <material name="">
        <color rgba="0.792156862745098 0.819607843137255 0.933333333333333 1" />
      </material>
    </visual>
    <collision>
      <origin xyz="0 0 0" rpy="0 0 0" />
      <geometry>
        <mesh filename="package://Final_light_assembly_URDF/meshes/lakat.STL" />
      </geometry>
    </collision>
  </link>
  <joint name="lakat" type="continuous">
    <origin xyz="0.32 0 0" rpy="3.1416 -6.3895E-16 -1.1753" />
    <parent link="nadlaktica" />
    <child link="lakat" />
    <axis xyz="0 0 -1" />
  </joint>
  <link name="podlaktica">
    <inertial>
      <origin xyz="0.015666 0.10444 0.04524" rpy="0 0 0" />
      <mass value="0.8658" />
      <inertia ixx="0.0043737" ixy="-0.00033248" ixz="-0.00029637" iyy="0.0017275" iyz="-0.0011009" izz="0.0039233" />
    </inertial>
    <visual>
      <origin xyz="0 0 0" rpy="0 0 0" />
      <geometry>
        <mesh filename="package://Final_light_assembly_URDF/meshes/podlaktica.STL" />
      </geometry>
      <material name="">
        <color rgba="0.79216 0.81961 0.93333 1" />
      </material>
    </visual>
    <collision>
      <origin xyz="0 0 0" rpy="0 0 0" />
      <geometry>
        <mesh filename="package://Final_light_assembly_URDF/meshes/podlaktica.STL" />
      </geometry>
    </collision>
  </link>
  <joint name="podlaktica" type="continuous">
    <origin xyz="0 -0.0735 0" rpy="-0.5648 -0.78173 1.7809" />
    <parent link="lakat" />
    <child link="podlaktica" />
    <axis xyz="0.14804 0.90477 0.39934" />
  </joint>
  <link name="saka">
    <inertial>
      <origin xyz="0.00102127447654127 0.00173769308862193 -0.00307332521672926" rpy="0 0 0" />
      <mass value="0.195660541483626" />
      <inertia ixx="0.000196163267087824" ixy="-1.19915207726741E-07" ixz="-4.99910323817217E-07" iyy="0.000195263940589931" iyz="9.07364788265256E-06" izz="0.000136132402412911" />
    </inertial>
    <visual>
      <origin xyz="0 0 0" rpy="0 0 0" />
      <geometry>
        <mesh filename="package://Final_light_assembly_URDF/meshes/saka.STL" />
      </geometry>
      <material name="">
        <color rgba="0.792156862745098 0.819607843137255 0.933333333333333 1" />
      </material>
    </visual>
    <collision>
      <origin xyz="0 0 0" rpy="0 0 0" />
      <geometry>
        <mesh filename="package://Final_light_assembly_URDF/meshes/saka.STL" />
      </geometry>
    </collision>
  </link>
  <joint name="saka" type="continuous">
    <origin xyz="0.037114 0.22683 0.10011" rpy="2.2965 -0.74045 -0.57161" />
    <parent link="podlaktica" />
    <child link="saka" />
    <axis xyz="-1 0 0" />
  </joint>
  <link name="hvataljka">
    <inertial>
      <origin xyz="0.00017222 0.00017758 0.00947" rpy="0 0 0" />
      <mass value="0.020284" />
      <inertia ixx="3.4622E-06" ixy="-9.927E-08" ixz="-2.2616E-08" iyy="3.4561E-06" iyz="-2.332E-08" izz="6.3508E-06" />
    </inertial>
    <visual>
      <origin xyz="0 0 0" rpy="0 0 0" />
      <geometry>
        <mesh filename="package://Final_light_assembly_URDF/meshes/hvataljka.STL" />
      </geometry>
      <material name="">
        <color rgba="0.79216 0.81961 0.93333 1" />
      </material>
    </visual>
    <collision>
      <origin xyz="0 0 0" rpy="0 0 0" />
      <geometry>
        <mesh filename="package://Final_light_assembly_URDF/meshes/hvataljka.STL" />
      </geometry>
    </collision>
  </link>
  <joint name="hvataljka" type="continuous">
    <origin xyz="0 0 -0.042312" rpy="-3.1416 2.5362E-15 0.2419" />
    <parent link="saka" />
    <child link="hvataljka" />
    <axis xyz="0 0 1" />
  </joint>
</robot>

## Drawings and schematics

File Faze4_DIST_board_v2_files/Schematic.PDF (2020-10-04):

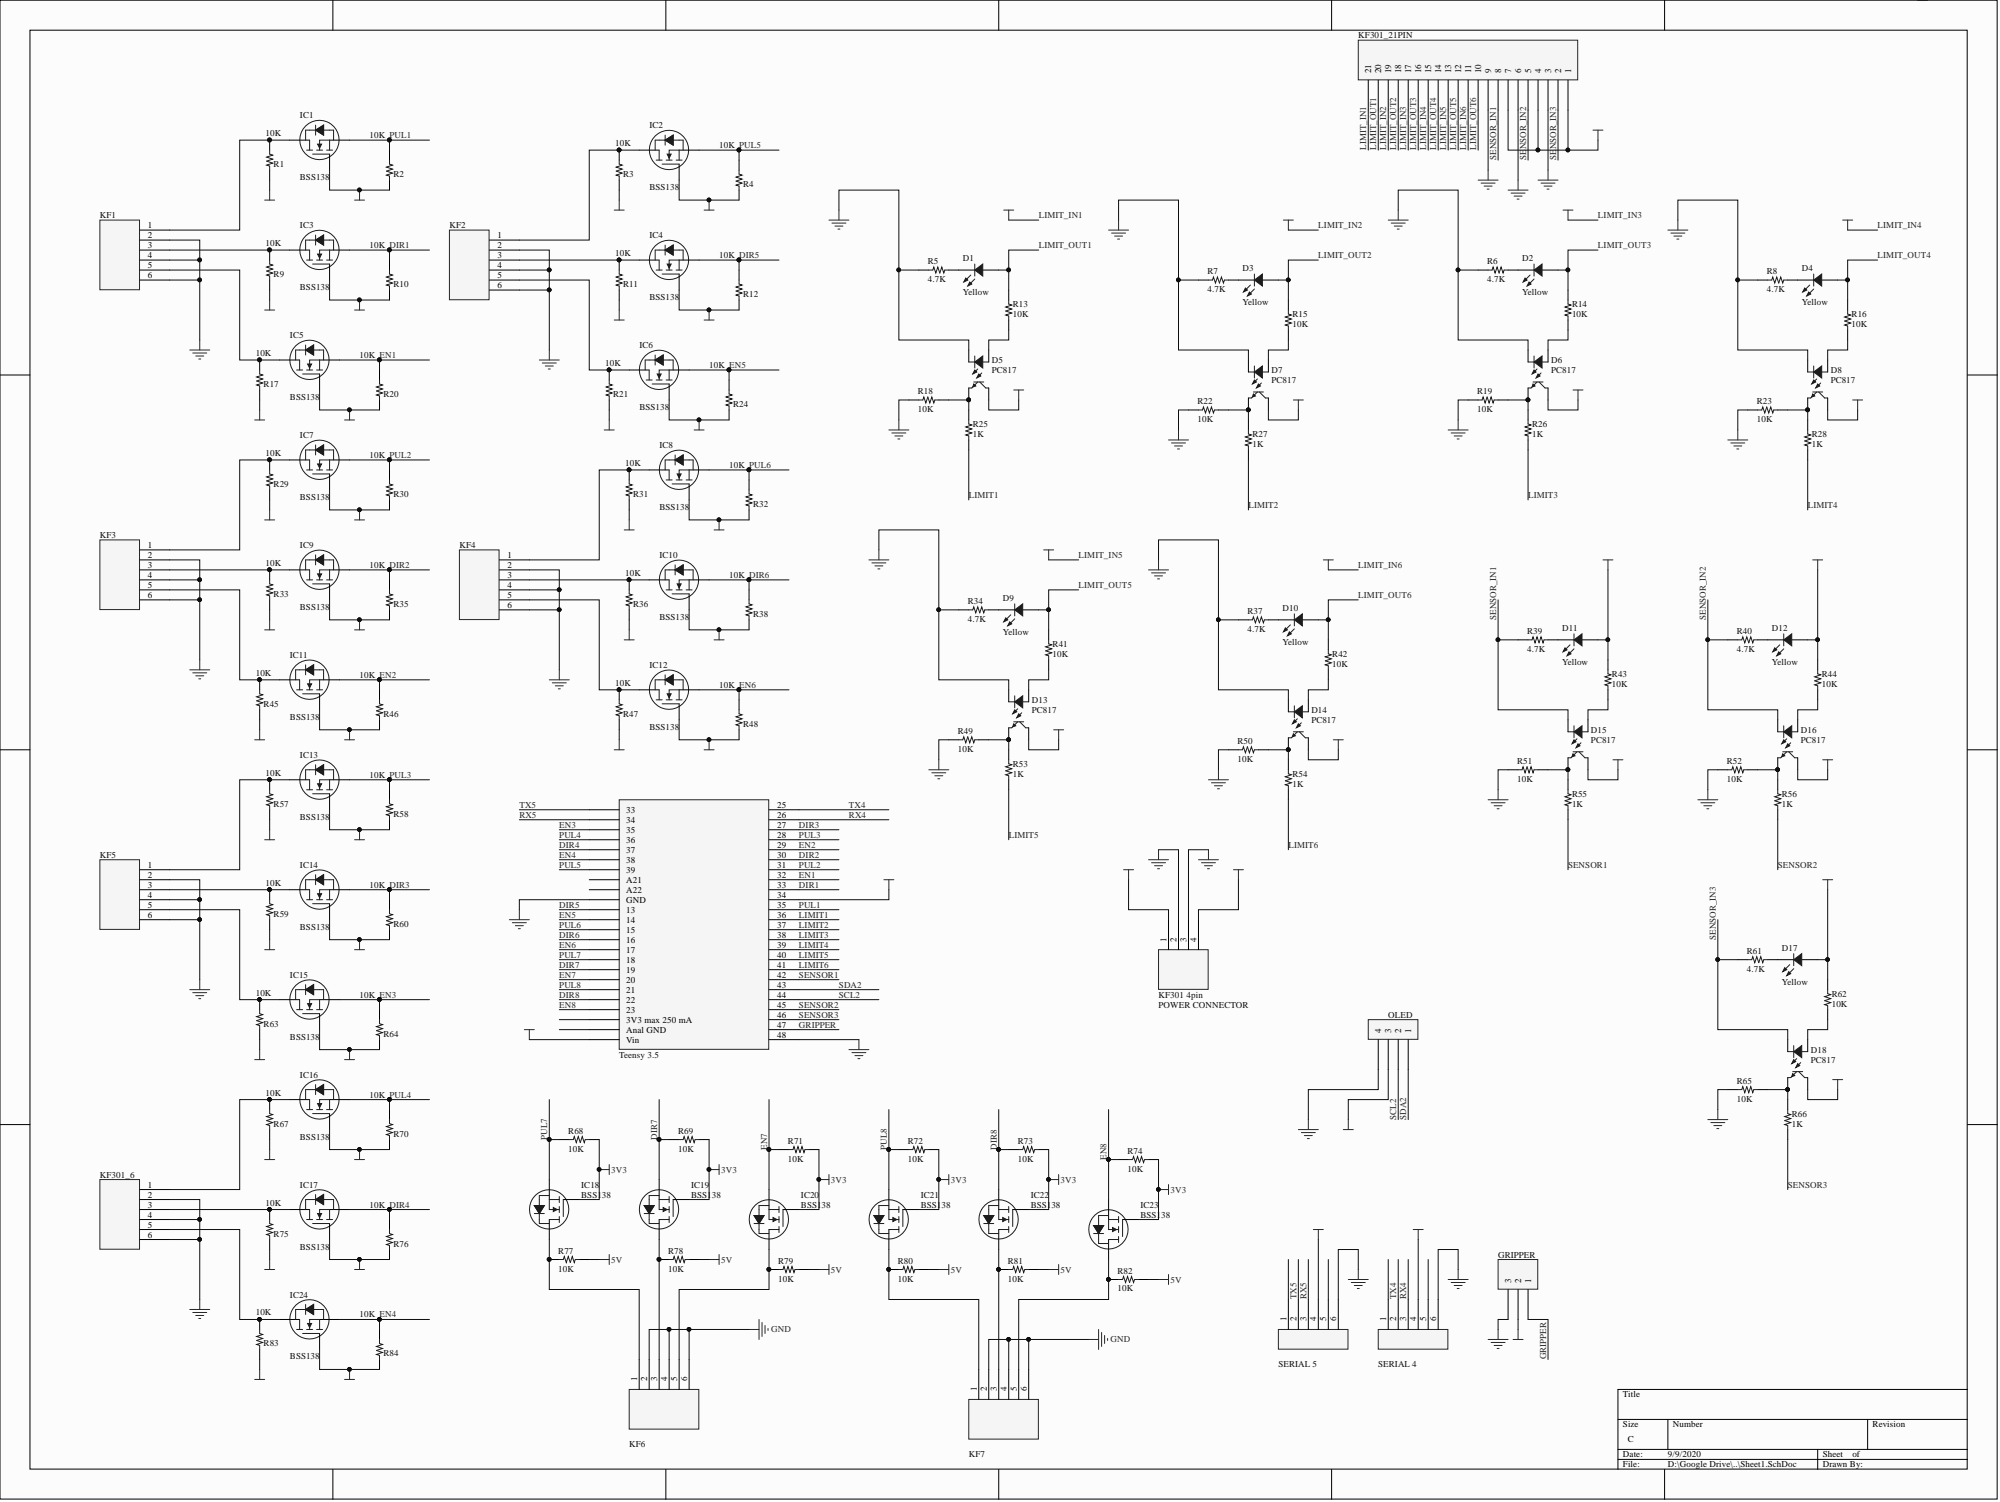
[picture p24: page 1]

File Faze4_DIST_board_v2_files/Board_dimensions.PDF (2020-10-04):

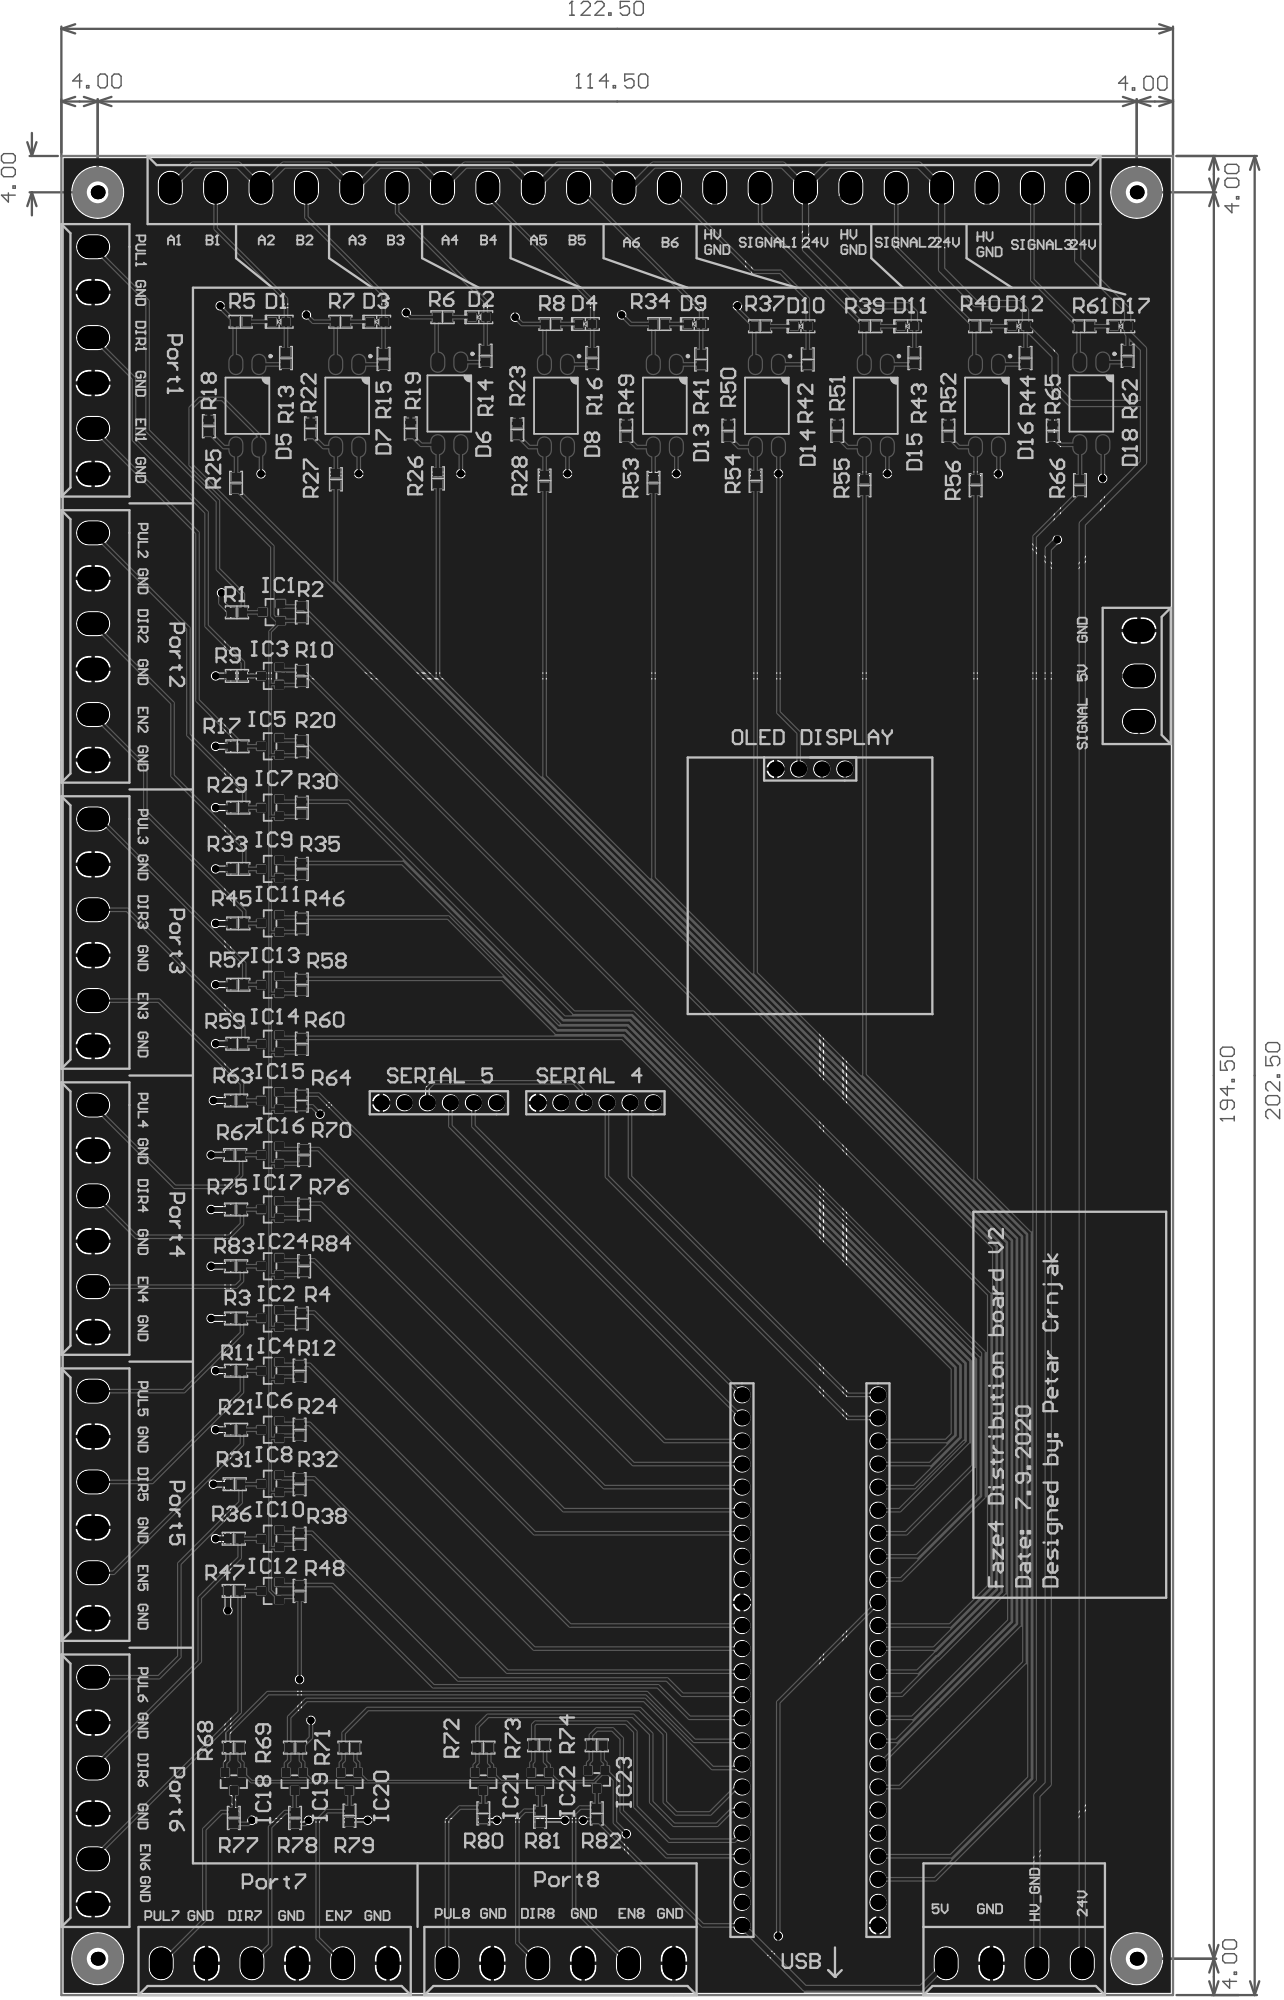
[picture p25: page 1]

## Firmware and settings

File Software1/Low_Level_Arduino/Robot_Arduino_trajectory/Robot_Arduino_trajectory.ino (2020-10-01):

/*************************************************************************
  By: Petar Crnjak
  version: 2.0
  For more info visit:
  https://github.com/PCrnjak/Faze4-Robotic-arm
**************************************************************************/

#include <Arduino.h>

/*****************************************************************************
  Define pins on pcb
  Defined by the name near the connector.
******************************************************************************/
#define pi 3.1415926535
// Joint6
// Port on PCB board P7
#define enable6 35    // port1  
#define dir6    36    // port2  
#define puls6   37    // port3  

// Joint5
//Port on PCB board P8 // On this connector pins for enable and puls are switched
// so our puls pin on board is connected to enable pin and our enable pin is connected to pulse pin
#define enable5 A21   // port6    
#define dir5    39    // port5  
#define puls5   38    // port4  

// Joint4
//
#define enable4 A22   // port7   analogWrite(A21, (int)val); rezolucija 12
#define dir4    13    // port8 // LED_BUILTIN  
#define puls4   14    // port9  

// Joint3
//Port on PCB board P12
#define enable3 15    // port10  
#define dir3    16    // port11  
#define puls3   17    // port12  

// Joint1
//Port on PCB board P16
#define enable1 20    // port13  
#define dir1    21    // port14  
#define puls1   22    // port15  

// Extra 1
//Port on PCB board P13
#define enable_ex1 2     // port16  
#define dir_ex1    1     // port17  
#define puls_ex1   0    // port18  

//Joint 2
//Port on PCB board P15
#define enable2 5     // port21  
#define dir2    4     // port20  
#define puls2   3     // port19  

// Extra 2
//Port on PCB board P14
#define enable_ex2 8     // port24  
#define dir_ex2    7     // port23  
#define puls_ex2   6     // port22  

//Port on PCB board P20
#define Gripper 23

//Inputs from left to right
#define limit2 28        // O1  
#define limit3 27        // O2  
#define limit4 26        // O3  
#define limit5 25        // O4  
#define limit_ex1 24     // O5  
#define limit_ex2 12     // O6  
#define limit_ex3 9      // O7   
#define limit1 10        // O8  
#define limit6 11        // O9   

// EXTRA PINS from top to bottom
// first is GND
#define ex1 29
#define ex2 30

int angle1[1000] = {};
int angle2[1000] = {};
int angle3[1000] = {};
int angle4[1000] = {};
int angle5[1000] = {};
int angle6[1000] = {};

int speed1[1000] = {};
int speed2[1000] = {};
int speed3[1000] = {};
int speed4[1000] = {};
int speed5[1000] = {};
int speed6[1000] = {};

const int EnablePin[] = {enable1, enable2, enable3, enable4, enable5, enable6}; // pins that enable stepper drivers

const int stepPin[] = {puls1, puls2, puls3, puls4, puls5, puls6}; // STEP pins on stepper drivers, first in array is joint 1, last i joint 6

const int dirPin[] = {dir1, dir2, dir3, dir4, dir5, dir6}; // DIR pins on stepper driver, first in array is joint 1 ,last is joint 6

const int LimitPin[] = {limit1, limit2, limit3, limit4, limit5, limit6}; // Pins for limit switches and inductive sensors

const int joint[7] = {0, 0, 1, 2, 3, 4, 5}; //// Calls---> Joint[1]=0 , Joint[2]=1...

const int meh_limit[] = {20000, 24000, 7000, 4000, 2600, 7700}; //Mechanical limits of joints.Represented in number of steps

const float gear_ratio[] = {25 , 27 , 15 , 11.847 , 11 , 19.19};

const float step_angle[] = {1.8 , 1.8 , 0.9 , 1.8 , 1.8 , 1.8};

const float microstep[] = {0.125 , 0.125 , 0.25 , 0.5 , 0.5 , 0.5};

bool zeroed[] = {0, 0, 0, 0, 0, 0}; // state variables that tell us if joint is zeroed or not

bool state[] = {0, 0, 0, 0, 0, 0}; // used in move_routine functions TODO test statis

unsigned long previousMillis[] = {0, 0, 0, 0, 0, 0};

int current_pulse_widht[] = {1000, 800, 1200, 900, 900, 900}; // current speed we are moving at

signed int current_position[] = {0, 0, 0, 0, 0, 0}; // our current position , never change this value manually after homing routine
signed int needed_position[] = {0, 0, 0, 0, 0, 0}; // position we want to go to

unsigned long currentMillis = 0;

volatile int error = 0; // Top level condition for robot to work , if 1 robot locks

uint16_t vars2[] = {0,0,0,0,0,0,0,0,0,0,0,0};

int m = 0;
int m_ = 0;
bool flag4 = 0;
bool flag5 = 0;

/*****************************************************************************
  Extra UART ports
 ******************************************************************************/
// RX5 = 34
// TX5 = 33
// RX4 = 31
// TX4 = 32

/*****************************************************************************
   OLED PINS
 ******************************************************************************/
// SDA = 18
// SCL = 19

/*****************************************************************************
    Prototype for used functions
 ******************************************************************************/
void Homing_routine(int joint_num);
void homeAll();
void move_all();
void move_routine_backward(int joint_num);
void move_routine_forward(int joint_num);
void false_swtich_trigger_function1(void);
void false_swtich_trigger_function2(void);
void false_swtich_trigger_function3(void);
void false_swtich_trigger_function4(void);
void false_swtich_trigger_function5(void);
void false_swtich_trigger_function6(void);
void get_data();
void robot_setup();
void get_data_2();
void data_test();
void first_pos();
void trajectory();

void setup() {

  Serial.begin(9600);
  while(!Serial){};
  Serial4.begin(9600);
  delay(1000);
  Serial4.println("Robot is starting , please wait");
  Serial4.println("...");
  Serial4.print("\n");

  delay(100);

  pinMode(LimitPin[joint[1]], INPUT_PULLUP);
  pinMode(EnablePin[joint[1]], OUTPUT);
  pinMode(stepPin[joint[1]], OUTPUT);
  pinMode(dirPin[joint[1]], OUTPUT);
  digitalWrite(dirPin[joint[1]], HIGH);

  pinMode(LimitPin[joint[2]], INPUT_PULLDOWN);
  pinMode(EnablePin[joint[2]], OUTPUT);
  pinMode(stepPin[joint[2]], OUTPUT);
  pinMode(dirPin[joint[2]], OUTPUT);
  digitalWrite(dirPin[joint[2]], HIGH);

  pinMode(LimitPin[joint[3]], INPUT_PULLDOWN);
  pinMode(EnablePin[joint[3]], OUTPUT);
  pinMode(stepPin[joint[3]], OUTPUT);
  pinMode(dirPin[joint[3]], OUTPUT);
  digitalWrite(dirPin[joint[3]], HIGH);

  pinMode(LimitPin[joint[4]], INPUT_PULLDOWN);
  pinMode(EnablePin[joint[4]], OUTPUT);
  pinMode(stepPin[joint[4]], OUTPUT);
  pinMode(dirPin[joint[4]], OUTPUT);
  digitalWrite(dirPin[joint[4]], HIGH);

  pinMode(LimitPin[joint[5]], INPUT_PULLDOWN);
  pinMode(EnablePin[joint[5]], OUTPUT);
  pinMode(stepPin[joint[5]], OUTPUT);
  pinMode(dirPin[joint[5]], OUTPUT);
  digitalWrite(dirPin[joint[5]], HIGH);

  pinMode(LimitPin[joint[6]], INPUT_PULLUP);
  pinMode(EnablePin[joint[6]], OUTPUT);
  pinMode(stepPin[joint[6]], OUTPUT);
  pinMode(dirPin[joint[6]], OUTPUT);
  digitalWrite(dirPin[joint[6]], HIGH);

  attachInterrupt(limit1, false_swtich_trigger_function1, FALLING);
  attachInterrupt(limit2, false_swtich_trigger_function2, RISING);
  attachInterrupt(limit3, false_swtich_trigger_function3, RISING);
  attachInterrupt(limit4, false_swtich_trigger_function4, RISING);
  attachInterrupt(limit5, false_swtich_trigger_function5, RISING);
  attachInterrupt(limit6, false_swtich_trigger_function6, FALLING);

  delay(5000);

  homeAll();

  detachInterrupt(limit1);
  detachInterrupt(limit2);
  detachInterrupt(limit3);
  detachInterrupt(limit4);
  detachInterrupt(limit5);
  detachInterrupt(limit6);

  current_pulse_widht[joint[1]] = 800;
  current_pulse_widht[joint[2]] = 900;
  current_pulse_widht[joint[3]] = 1200;
  current_pulse_widht[joint[4]] = 900;
  current_pulse_widht[joint[5]] = 900;
  current_pulse_widht[joint[6]] = 900;

 
  //Serial4.begin(9600);
  delay(1000);
  //Serial4.println("Robot is starting , please wait");
  //Serial4.println("...");
  //Serial4.print("\n");


}

void loop() {
  robot_setup();
  //data_test();
  first_pos();
  delay(1000);
  // goto first position
  while (error == 0) {
    //get_data();
    //move_all();
    trajectory();

  }
}


  void homeAll() {

    int flag = 0;
    /*****************************************************************************
      detach interrupts , if we dont do this robot will lock itself up
      ******************************************************************************/
    detachInterrupt(limit1);
    detachInterrupt(limit2);
    detachInterrupt(limit3);
    detachInterrupt(limit4);
    detachInterrupt(limit5);
    detachInterrupt(limit6);
    /*****************************************************************************
      Set speed for homing routines
    ******************************************************************************/
    current_pulse_widht[joint[1]] = 1500;
    current_pulse_widht[joint[2]] = 1500;
    current_pulse_widht[joint[3]] = 1500;
    current_pulse_widht[joint[4]] = 1500;
    current_pulse_widht[joint[5]] = 1500;
    current_pulse_widht[joint[6]] = 1500;
    /*****************************************************************************
        Enable all motors TODO joints that are on DACS
     ******************************************************************************/

    digitalWrite(EnablePin[joint[1]], LOW);
    delay(200);
    digitalWrite(EnablePin[joint[2]], LOW);
    delay(200);
    digitalWrite(EnablePin[joint[3]], LOW);
    delay(200);
    analogWrite(EnablePin[joint[5]], 0);
    delay(200);
    analogWrite(EnablePin[joint[4]], 0);
    delay(200);
    digitalWrite(EnablePin[joint[6]], LOW);

    /*****************************************************************************
         Set direction for all motors
    ******************************************************************************/
    digitalWrite(dirPin[joint[1]], HIGH);
    digitalWrite(dirPin[joint[2]], HIGH);
    digitalWrite(dirPin[joint[3]], HIGH);
    digitalWrite(dirPin[joint[4]], HIGH);
    digitalWrite(dirPin[joint[5]], HIGH);
    digitalWrite(dirPin[joint[6]], LOW);

    /*****************************************************************************
      Home joints 6 ,5 and 4
    ******************************************************************************/
    int i = 0;
    while ((zeroed[joint[6]] != 1)  or (zeroed[joint[5]] != 1) or (zeroed[joint[4]] != 1)) {

      Homing_routine(joint[4]);
      Homing_routine(joint[5]);
      Homing_routine(joint[6]);

      /*****************************************************************************
        Robot lock
      ******************************************************************************/
      //while (flag == 1) {}

      /*****************************************************************************
         check if we are moving to much to home the motor
         if we do lock the robot
         ******************************************************************************/
      for (i = 4; i < 7; i++) {
        if ((current_position[joint[i]] + 50) >= meh_limit[joint[i]]) {
          Serial4.println("Error: It took too long for joint ");
          Serial4.print(i);
          Serial4.print(" s limit switch to trigger, restart your controller");
          flag = 1;
          break;

        }

      }

    }

    /*****************************************************************************
       Set current positions to 0 since we hit our homing switches
    ******************************************************************************/
    current_position[joint[6]] = 75;
    current_position[joint[5]] = 0;
    current_position[joint[4]] = 0;
    delay(500);
    /*****************************************************************************
      Now we will move from those limit switches for specific amounts
       We are doing this so that robot will never hit limit switches in normal operation
      In the same step we also move them to standby position              (this is position in kinematics
        diagram where all joints are in 0 position)
       We dont need to offset joint 6 since it is continous rotation joint
      We offset current position by :
      .  *            Joint 5 = offset 110 = new 0 , standby positon new = 1173
                  Joint 4 = offset 110 = new 0 , standby positon new = 2275
    ******************************************************************************/
    needed_position[joint[6]] = 0;

    needed_position[joint[5]] = 1283;

    needed_position[joint[4]] = 2385;

    while (needed_position[joint[6]] != current_position[joint[6]] or needed_position[joint[5]] != current_position[joint[5]] or needed_position[joint[4]] != current_position[joint[4]] ) {
      move_all();

    }

    /*****************************************************************************
       These positons represent robot in its standby position
       This position would be 0 positions in robot kinematic diagram.
    ******************************************************************************/
    current_position[joint[6]] = 3838;
    needed_position[joint[6]] = 3838;

    current_position[joint[5]] = 1173;
    needed_position[joint[5]] = 1173;

    current_position[joint[4]] = 2275;
    needed_position[joint[4]] = 2275;

    /*****************************************************************************
         Home only joint 3
     ******************************************************************************/
    delay(200);
    while ((zeroed[joint[3]] != 1)) {
      Homing_routine(joint[3]);
      while (flag == 1) {}
      if ((current_position[joint[3]] + 50) >= meh_limit[joint[3]]) {
        Serial4.println("Error: It took too long for joint ");
        Serial4.print(3);
        Serial4.print(" s limit switch to trigger, restart your controller");
        flag = 1;
        break;

      }

    }

    /*****************************************************************************
      Here we only move from limit switch , and will later move with joint 2 to
       standby position
     ******************************************************************************/

    delay(100);
    current_position[joint[3]] = 0;
    needed_position[joint[3]] = 350;

    while (needed_position[joint[3]] != current_position[joint[3]]  ) {
      move_all();

    }
    current_position[joint[3]] = 0;
    needed_position[joint[3]] = 0;

    /*****************************************************************************
      Home only joint 2
    ******************************************************************************/
    delay(200);
    while ((zeroed[joint[2]] != 1)) {
      Homing_routine(joint[2]);
      //while (flag == 1) {}
      if ((current_position[joint[2]] + 50) >= meh_limit[joint[2]]) {
        Serial4.println("Error: It took too long for joint ");
        Serial4.print(2);
        Serial4.print(" s limit switch to trigger, restart your controller");
        flag = 1;
        break;

      }

    }

    /*****************************************************************************
       Here we only move from limit switch , and will later move with joint 3 to
      standby position
    ******************************************************************************/

    delay(100);
    current_position[joint[2]] = 0;
    needed_position[joint[2]] = 700;

    while (needed_position[joint[2]] != current_position[joint[2]] ) {
      move_all();

    }

    current_position[joint[2]] = 0;
    needed_position[joint[2]] = 0;

    /*****************************************************************************
      Home only joint 1
    ******************************************************************************/

    delay(200);
    while ((zeroed[joint[1]] != 1)) {
      //while (flag == 1) {}
      Homing_routine(joint[1]);
      if ((current_position[joint[1]] + 50) >= meh_limit[joint[1]]) {
        Serial4.println("Error: It took too long for joint ");
        Serial4.print(1);
        Serial4.print(" s limit switch to trigger, restart your controller");
        flag = 1;
        break;

      }

    }

    delay(100);
    current_position[joint[1]] = 10000;
    needed_position[joint[1]] = 9500; //10500
    delay(5);

    while (needed_position[joint[1]] != current_position[joint[1]]  ) {
      move_all();

    }

    current_position[joint[1]] = 10000;
    needed_position[joint[1]] = 10000;

    /*****************************************************************************
       Move joints 2 and 3 to standby positons
      .  ******************************************************************************/
    digitalWrite(dirPin[joint[2]], LOW);
    needed_position[joint[2]] = 10000 ;

    digitalWrite(dirPin[joint[3]], LOW);
    needed_position[joint[3]] = 2650;

    while (needed_position[joint[2]] != current_position[joint[2]] or needed_position[joint[3]] != current_position[joint[3]]) {
      move_all();

    }

    /*****************************************************************************
      Attach interrupts
      They should never activate in normal operation
      We do not attach interrupts for limit 1 and 6
    ******************************************************************************/

    //attachInterrupt(limit1, false_swtich_trigger_function1, FALLING);
    attachInterrupt(limit2, false_swtich_trigger_function2, RISING);
    attachInterrupt(limit3, false_swtich_trigger_function3, RISING);
    attachInterrupt(limit4, false_swtich_trigger_function4, RISING);
    attachInterrupt(limit5, false_swtich_trigger_function5, RISING);
    //attachInterrupt(limit6, false_swtich_trigger_function6, FALLING);

  }

  /*****************************************************************************
    Similar to move forward/backward but has extra steps
      to check if switches are pressed
  ******************************************************************************/
  void Homing_routine(int joint_num) {
    if (digitalRead(LimitPin[joint_num]) == LOW) {
      currentMillis = micros();
      //// state is used to prevent triggering of this if statement twice in row
      ///// same goes for second one , this secures perfect square wave form
      if (currentMillis - previousMillis[joint_num] >= current_pulse_widht[joint_num] and state[joint_num] == 0) {
        previousMillis[joint_num] = currentMillis;
        digitalWrite(stepPin[joint_num], HIGH);
        state[joint_num] = 1;

      }
      else if (currentMillis - previousMillis[joint_num] >= current_pulse_widht[joint_num] and state[joint_num] == 1) {
        previousMillis[joint_num] = currentMillis;
        digitalWrite(stepPin[joint_num], LOW);
        state[joint_num] = 0;
        current_position[joint_num] = current_position[joint_num] + 1;


      }

    }
    if (digitalRead(LimitPin[joint_num]) == HIGH and zeroed[joint_num] == 0 ) {
      current_position[joint_num] = 0;
      Serial4.println("Joint ");
      Serial4.print(joint_num + 1);
      Serial4.println(" in 0 position.");
      zeroed[joint_num] = 1;

    }

  }

  /*****************************************************************************
    Function that checks if we are at desired position
      If we are not move until we are
   ******************************************************************************/
  void move_all() {

    if (needed_position[joint[1]] > current_position[joint[1]] ) {
      digitalWrite(dirPin[joint[1]], LOW);
      move_routine_forward(joint[1]);

    }
    else if (needed_position[joint[1]] < current_position[joint[1]] ) {
      digitalWrite(dirPin[joint[1]], HIGH);
      move_routine_backward(joint[1]);

    }
    if (needed_position[joint[2]] > current_position[joint[2]] ) {
      digitalWrite(dirPin[joint[2]], LOW);
      move_routine_forward(joint[2]);

    }
    else if (needed_position[joint[2]] < current_position[joint[2]] ) {
      digitalWrite(dirPin[joint[2]], HIGH);
      move_routine_backward(joint[2]);

    }
    if (needed_position[joint[3]] > current_position[joint[3]]) {
      digitalWrite(dirPin[joint[3]], LOW);
      move_routine_forward(joint[3]);

    }
    else if (needed_position[joint[3]] < current_position[joint[3]] ) {
      digitalWrite(dirPin[joint[3]], HIGH);
      move_routine_backward(joint[3]);

    }
    if (needed_position[joint[4]] > current_position[joint[4]] ) {
      digitalWrite(dirPin[joint[4]], LOW);
      move_routine_forward(joint[4]);

    }
    else if (needed_position[joint[4]] < current_position[joint[4]] ) {
      digitalWrite(dirPin[joint[4]], HIGH);
      move_routine_backward(joint[4]);

    }
    if (needed_position[joint[5]] > current_position[joint[5]] ) {
      digitalWrite(dirPin[joint[5]], LOW);
      move_routine_forward(joint[5]);

    }
    else if (needed_position[joint[5]] < current_position[joint[5]]) {
      digitalWrite(dirPin[joint[5]], HIGH);
      move_routine_backward(joint[5]);

    }
    if (needed_position[joint[6]] > current_position[joint[6]] ) {
      digitalWrite(dirPin[joint[6]], HIGH);
      move_routine_forward(joint[6]);

    }
    else if (needed_position[joint[6]] < current_position[joint[6]] ) {
      digitalWrite(dirPin[joint[6]], LOW);
      move_routine_backward(joint[6]);

    }

  }

  /*****************************************************************************
      Routine to move forward
   ******************************************************************************/
  void move_routine_forward(int joint_num) {
    currentMillis = micros();
    ///state is used to prevent triggering of this if statement twice in row
    // same goes for second one , this secures perfect square wave form
    if (currentMillis - previousMillis[joint_num] >= current_pulse_widht[joint_num] and state[joint_num] == 0) {
      previousMillis[joint_num] = currentMillis;
      digitalWrite(stepPin[joint_num], HIGH);
      state[joint_num] = 1;

    }
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

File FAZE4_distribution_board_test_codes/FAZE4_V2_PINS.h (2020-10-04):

#define LIMIT1 11
#define LIMIT2 10
#define LIMIT3 9
#define LIMIT4 8
#define LIMIT5 7
#define LIMIT6 6
#define SENSOR1 5
#define SENSOR2 2
#define SENSOR3 1


#define PUL1 12
#define DIR1 24
#define ENA1 25

#define PUL2 26
#define DIR2 27
#define ENA2 28

#define PUL3 29
#define DIR3 30
#define ENA3 35

#define PUL4 36
#define DIR4 37
#define ENA4 38

#define PUL5 39
#define DIR5 13
#define ENA5 14

#define PUL6 15
#define DIR6 16
#define ENA6 17

#define PUL7 18
#define DIR7 19
#define ENA7 20

#define PUL8 21
#define DIR8 22
#define ENA8 23

#define GRIPPER 0

#define SDA_2 43
#define SCL_2 44

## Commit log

2019-08-21 Added STL files
2020-05-04 add URDF files for robotic arm
    [Final_light_assembly_URDF.urdf, hvataljka.STL, lakat.STL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]
2020-07-03 Delete STL.zip
    added new updated version
2020-07-03 Added Joint 2 limit trigger STL, base wire holder and fix for joint 2 cyclo
2020-07-04 Added updated BOM
    [Bom_1.2_joint2_update.xlsx]
2023-10-31 UPDATED BOM
    [BOM_31_10_2023.xlsx]

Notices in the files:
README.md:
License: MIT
